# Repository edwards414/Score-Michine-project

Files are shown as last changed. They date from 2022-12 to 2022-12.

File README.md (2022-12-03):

# IoT Score Machine:Deep Leaning to predict score machine 
> **學校專題-成績辨識器**
>
> 影片介紹: [執行畫面](https://www.youtube.com/watch?v=YyPfOn3d-Wk)
>
>研究動機: 為改善目前登記成績的速度以及大資料的整理



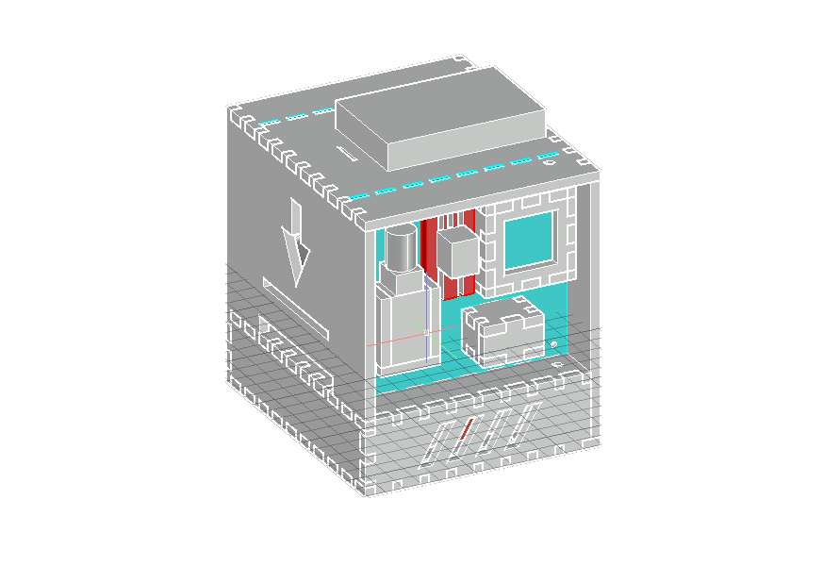
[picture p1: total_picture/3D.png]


## 結構設計
>   
> 設計 : [分解環繞影片](https://www.youtube.com/watch?v=SSCol9JbORs)
> 
在影片中我的捲軸系統是利用兩串小輪胎加上齒輪然後使用減速馬達將它帶動,辨識區域是利用伺服馬達來控制倒紙作業,整個結構是利用雷射切割完成,使用的軟體是AutoCAD,整個作品使用了2D組裝的思維藉由卡扣連接設計進行
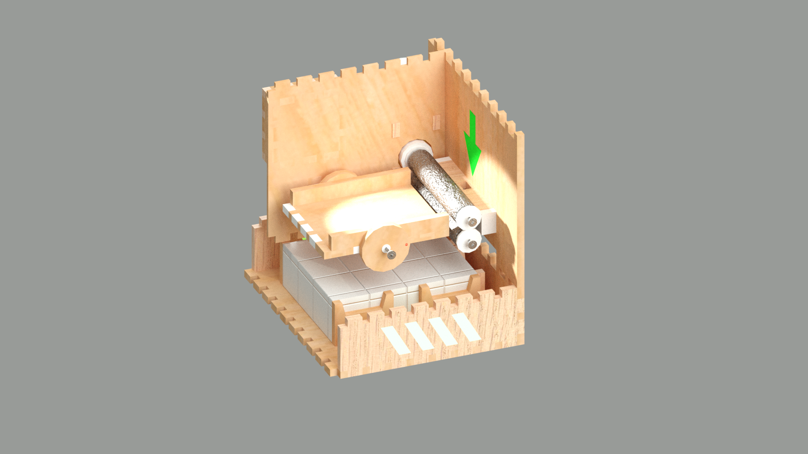
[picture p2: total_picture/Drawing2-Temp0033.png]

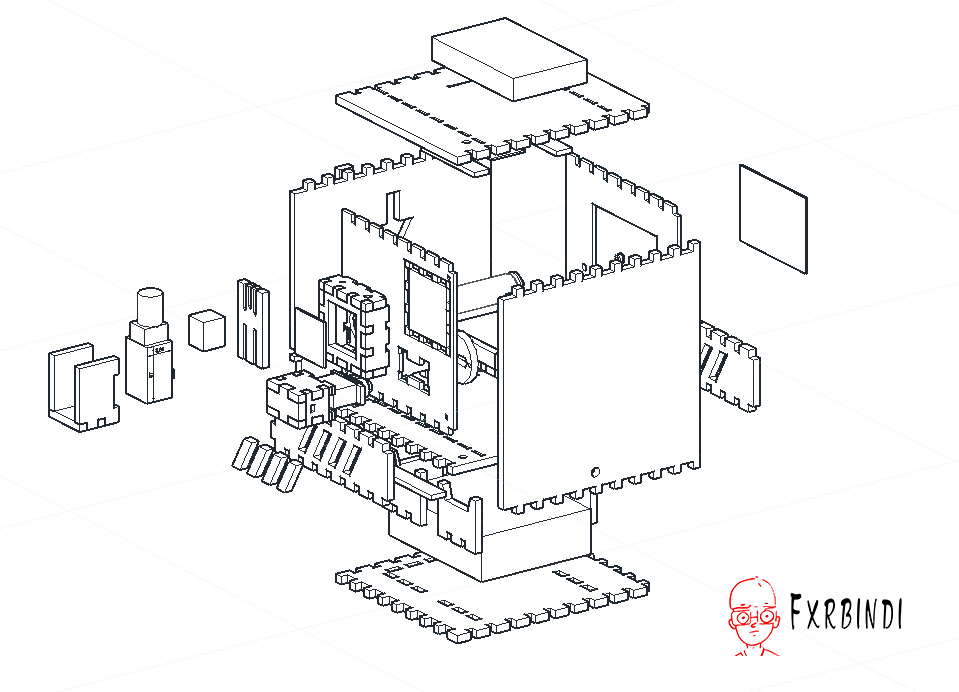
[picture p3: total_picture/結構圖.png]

> 草稿圖

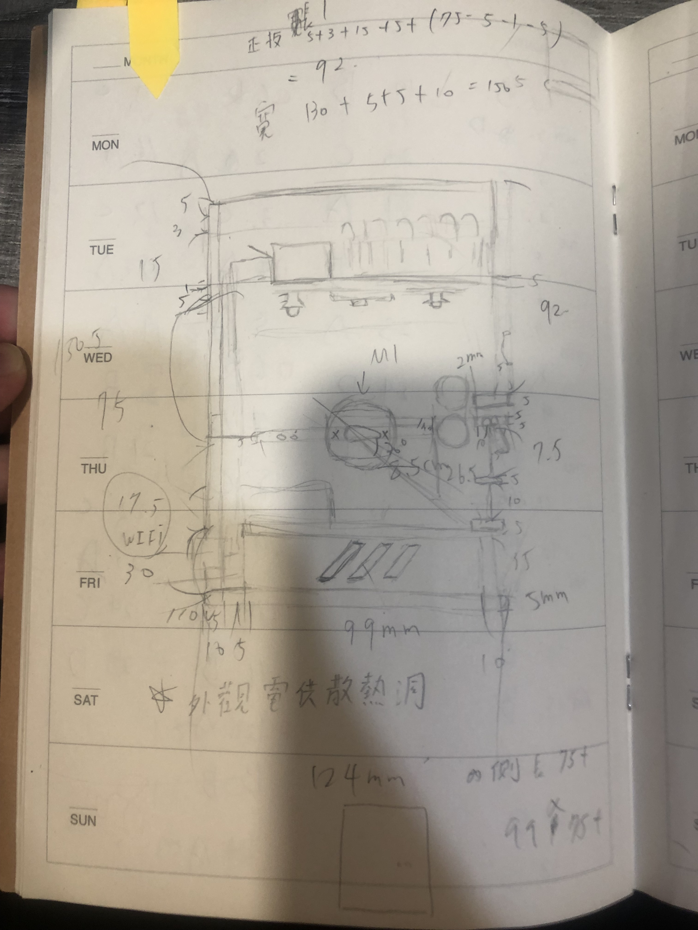
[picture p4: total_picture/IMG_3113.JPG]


> 捲軸系統

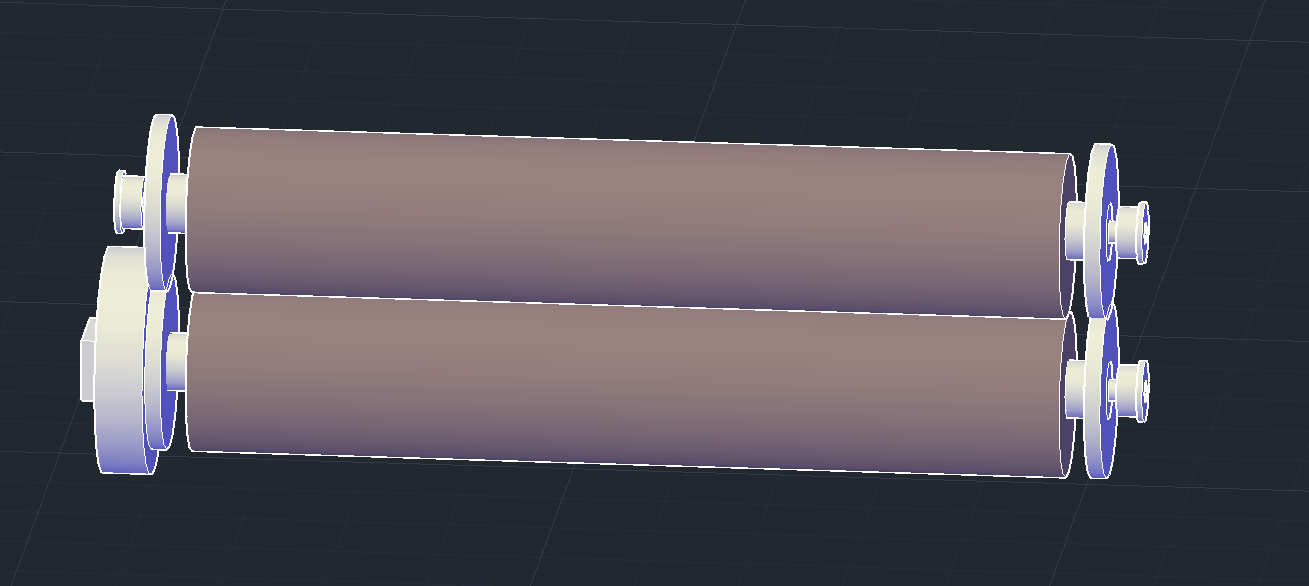
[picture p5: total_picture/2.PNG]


## 使用器具

- 主要硬體
  - Raspberry pi 3b+
  - 減速馬達
  - 伺服馬達(mg90s)180度
  - 3.3v 轉5v電位邏輯轉換器(T74)
  - 紅外線巡跡模組(FC123) *2
  - LED燈條(WS2812)*4
  - 繼電器5v
  - AC110-DC5V電源供應
- 軟體
  - Visual Studio Code
  - AutoCad
  - Adobe Illustrator 2022
  - Adobe Photoshop 2021
  - FileZilla
- 語言
  - python
  - javascript
  - html
  - css
  - javascript
  - bootscript

## 網頁設計
 
我使用了google-excel(當成資料庫),利用javascript讀取資料庫並在網頁上面呈現,網頁可以對成績表做查詢,也做RWD設計讓各個裝置都可以使用

> 網站介紹: [點我!!查詢請輸入【段考二】](https://script.google.com/macros/s/AKfycbwUPB8av8gJiDm0B71revtbjKE4klsRZkYY4DOG9oE/dev)

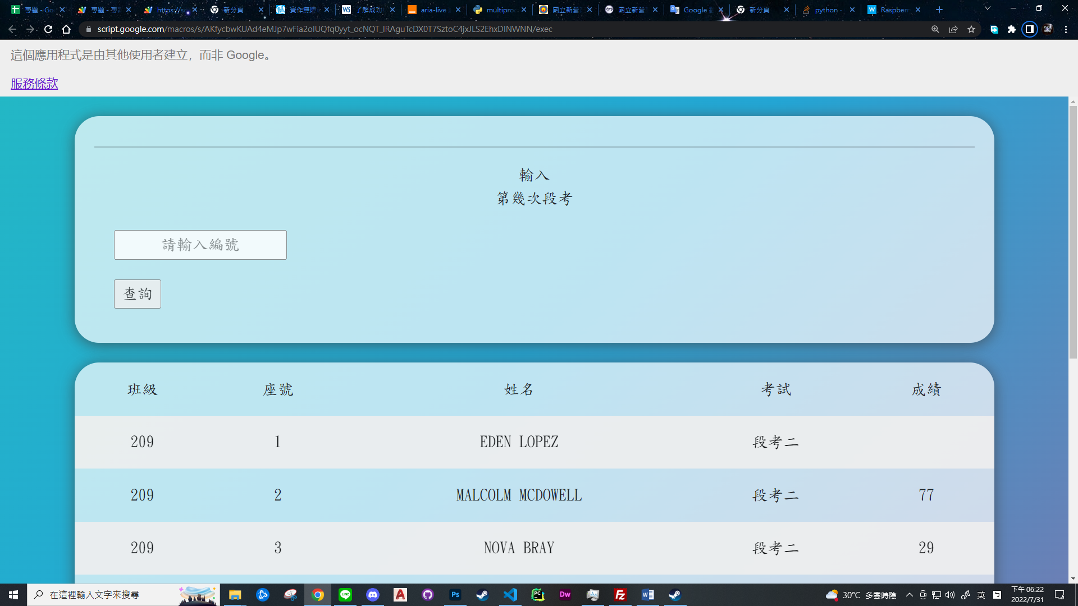
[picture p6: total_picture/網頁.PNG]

> 
>使用google-api讓python能與google-excel連結
>

## 使用方法/示例

```python
gc = pygsheets.authorize(service_account_file='project.json')
survey_url = 'your google-excel url'
sh = gc.open_by_url(survey_url)
ws = sh.worksheet_by_title('text')#你的試算表名稱
```
取得憑證(.join的檔案)後,python讀取join檔後利用這個檔案與google-api進行驗證,之後就可以操控試算表了

> [原作網址](https://hackmd.io/@Yun-Cheng/GoogleSheets)

## 關於辨識系統
> 深度學習
> 卷積神經網路(Convoluational Neural Network)
> 訓練庫 經典的手寫數字資料集【Mnist】

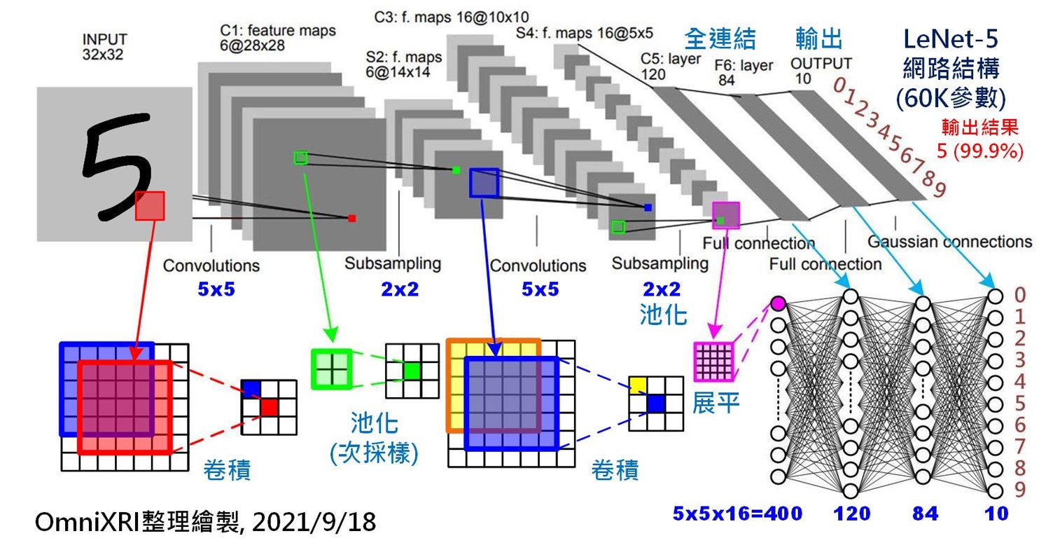
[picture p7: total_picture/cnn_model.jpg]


- [原作:OmniXRI](https://ithelp.ithome.com.tw/m/articles/10266628?sc=rss.iron)

Cnn是用來影像辨識的,它的功能用起來就像,假如我們看見一個人我們要怎麼判斷是不是人,在我們的大腦中,眼睛會先透過把看見的東西傳回腦袋,然後我們的大腦會進行特徵的擷取並與我們認知人的特徵做對比,進行對比後發現有部分軌跡形狀相似,我們就會認為他是一個人,在電腦中是輸入,卷積層,池化層,卷積層,池化層,壓平,傳入神經元進行分析輸出0-9的機率

如何在python中使用cnn,我們會在程式中建立cnn模型,把圖片正規化,後把資料丟進去訓練,把訓練完的權重(Weights)儲存,再用訓練好的權重套到(load_weights)模型上對圖片進行預測(predict)

> 卷積模型(model)

```python
def CNN_model():
    model = keras.Sequential(name="CNN") 
    model.add(layers.Conv2D(16,(5,5),activation='relu',padding='same',input_shape=(28,28,1))) #第一層輸入
    model.add(layers.MaxPooling2D((2,2)))
    model.add(layers.Conv2D(32,(5,5),padding='same',activation='relu'))
    model.add(layers.MaxPooling2D((2,2)))
    model.add(layers.Dropout(0.25))
    model.add(layers.Flatten())#轉一維陣列
    model.add(layers.Dense(128,activation="relu"))
    model.add(layers.Dropout(0.5))
    model.add(layers.Dense(10,activation='softmax')) #0-9輸出
    model.compile(optimizer='adam',
               loss=tf.losses.SparseCategoricalCrossentropy(from_logits=True),
               metrics=['acc'])
    return model
```
> 訓練結果

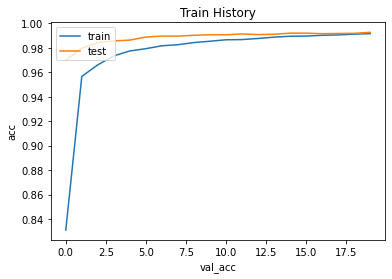
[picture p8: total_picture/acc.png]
  
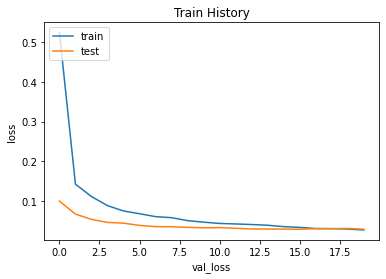
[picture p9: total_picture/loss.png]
   

> 驗證正規化(Normalization)的過程
正規化是一個在進入卷積神經網路模型之前的一個程序主要工作是將圖片改成固定格式的二維陣列

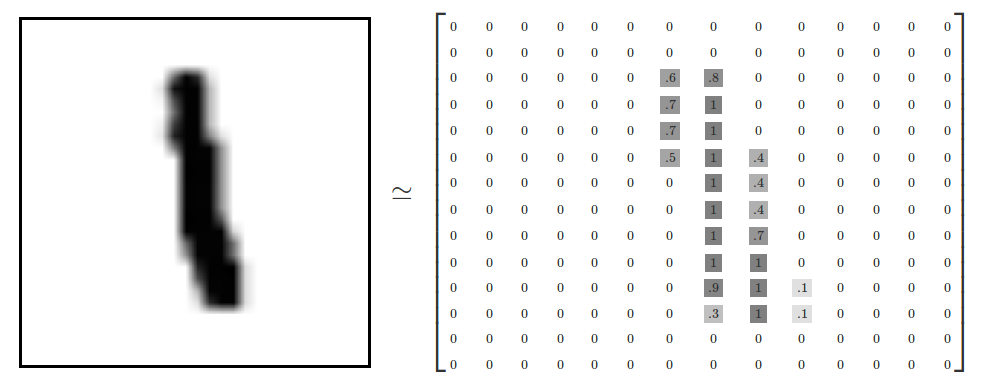
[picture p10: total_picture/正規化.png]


>為什麼要求證?

A:因為在進行卷積模型訓練時,我發現我丟我自己的圖片進入cnn_model進行預測,預測出來的答案與我寫的數字不一樣所以我針對正規化這個部分下去做驗證看是否在input時就有問題了

> 
> 我使用了python把程式中正規化的部分逐一填入excel
> 
> 這樣就可以在excel中圖像化
> 
> 在編輯器中無法將正規化print出來所以才使用excel作為輔助

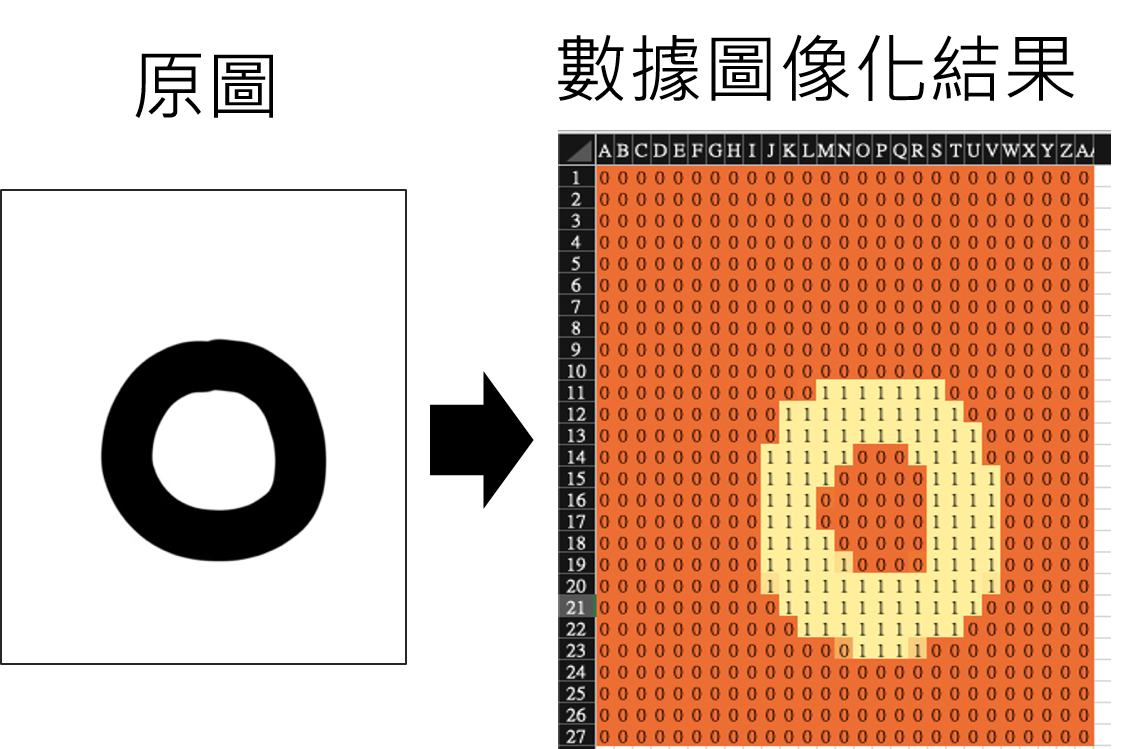
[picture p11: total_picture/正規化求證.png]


## 影像處理 

- 紙張進入後利用綠光加藍光把紅色變成黑色之後用高對比把線條的輪廓加深

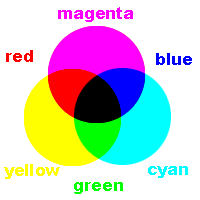
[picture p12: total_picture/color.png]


- 經過侵蝕圖片的方式把小點都處理掉

- 取得圖片的輪廓進行正方形的截圖

- 對每個數字切割

> 拍攝紙張

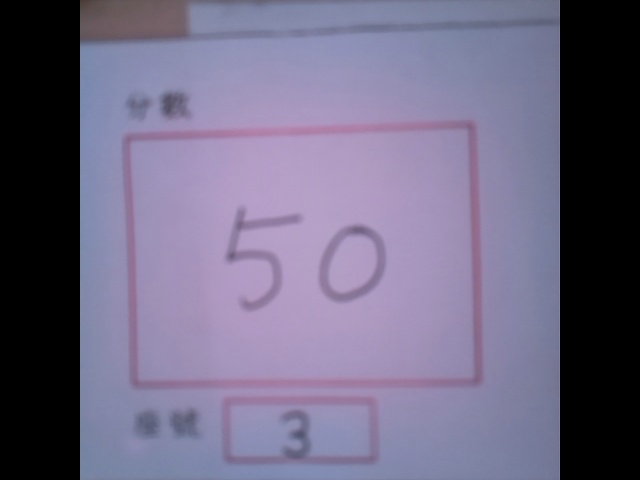
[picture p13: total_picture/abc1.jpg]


> 處理

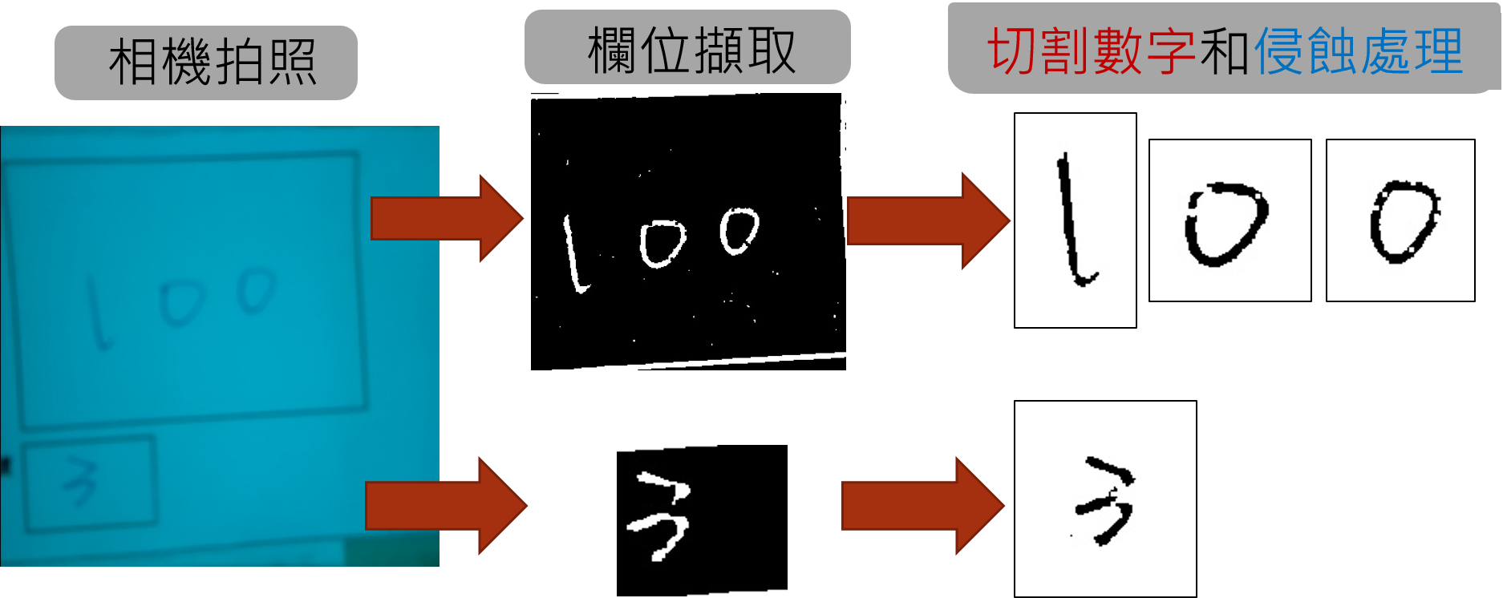
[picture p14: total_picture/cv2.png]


本來是用HSV下去做顏色的判斷後來發現不管怎麼調,截出來圖片都是一團亂,也有用YUV色彩去抓顏色,也是因為YUV對紅色及藍色有較好的辨識度所以才會用紅框,後來調光源發現在白光的照亮下我的圖上白色的部分有很多的粉紅色的光影,所以就朝著透過光源的方向去讓圖片處理得更好 

更好的方式:霍華夫取線(是一個ai對直線的算法,使用這個算法可以使圖片提取更完整)
## 線路圖

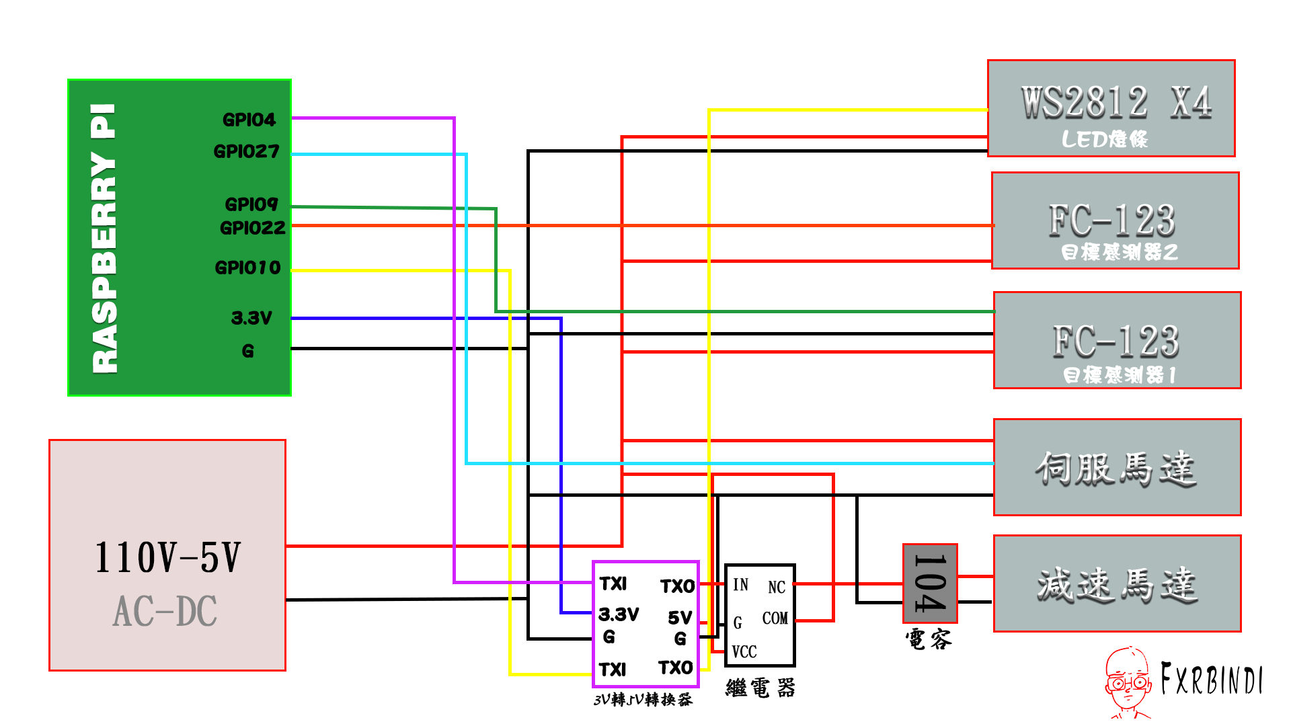
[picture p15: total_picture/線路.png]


> CAD模擬各零件擺放

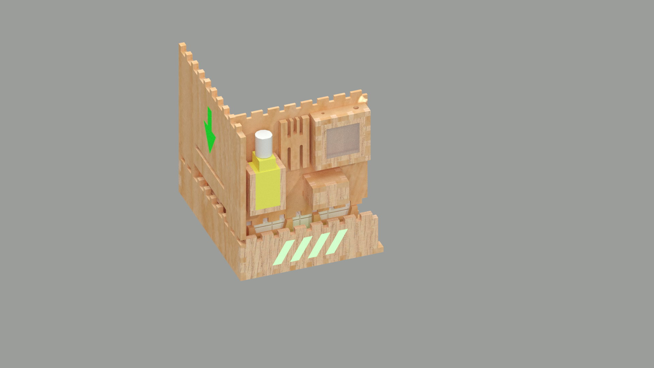
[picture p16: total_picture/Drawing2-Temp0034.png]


> 實際主裝

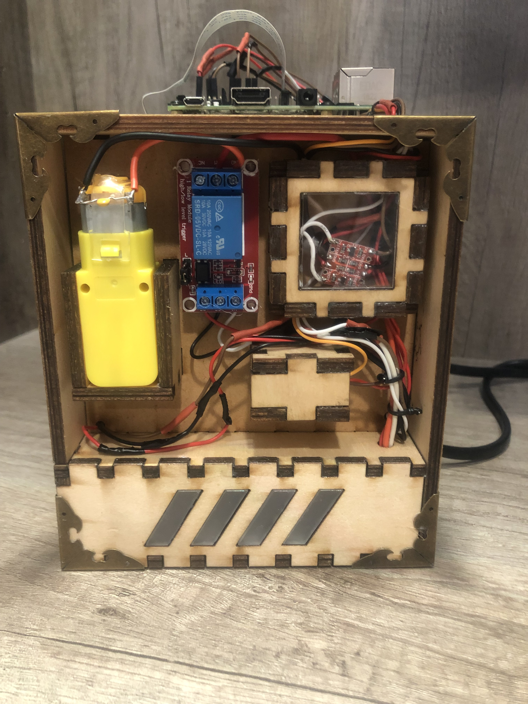
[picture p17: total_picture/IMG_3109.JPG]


## 流程程式

> 初始化
> 
> 接著呼叫FC123 loop定義
> 
> 執行拍照截圖處理..等程序
> 
> except除錯程序控制燈號警示我們
> 

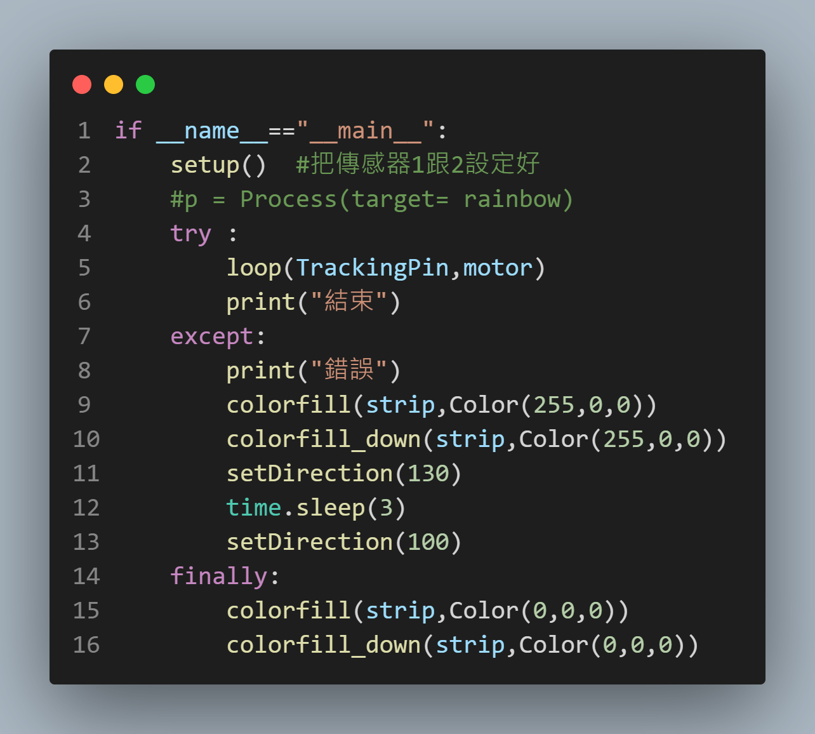
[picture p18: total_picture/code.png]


## 處理問題

> 伺服馬達抖動問題
> 
> WS2812 LED燈條五秒鐘後出現白光-不受控制
> 
> PMIC 損毀

### 1.伺服馬達抖動問題

> 可能的問題是軟體模擬pwm波會有誤差值,每一個伺服馬達的誤差值都不一樣,假如開發版發出來的誤差值大於伺服馬達給出的誤差值就會出現抖動的問題

我們一剛開始應先從程式的部分下手,因為我們所用的mg90s它是屬於較便宜的馬達所以它的誤差值沒有像步進馬達那些更高階的馬達小,所以不太會因為誤差而抖動

伺服馬達的功能與金錢成正比!!

> 伺服馬達原理(型號：mg90s)

伺服馬達是利用pwm去控制轉舵要轉幾度

 > 什麼是pwm ? 

分為硬體pwm、軟體pwm控制(現在使用的是軟體pwm)

 led燈有開跟關兩個狀態我們都是利用pin腳輸出高電壓(3.3v)或者低電壓(0v)來控制,但我們的伺服馬達有0～180度有180種狀態,所以就要使用pwm作為控制,pwm也是一種輸出高低電壓的原理,但他是使用高低電壓的時間差作為一種訊號

電源頻率50HZ,脈衝寬度500us-2500us 

1s = 1000ms ,1ms = 1000us

我們由電源頻率得知工作週期為20ms

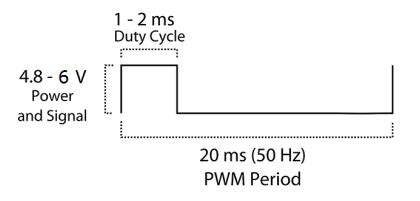
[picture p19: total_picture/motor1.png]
 

伺服馬達脈衝寬度調變訊號
（Servo PWM Singal）

各角度所需要的脈衝寬度

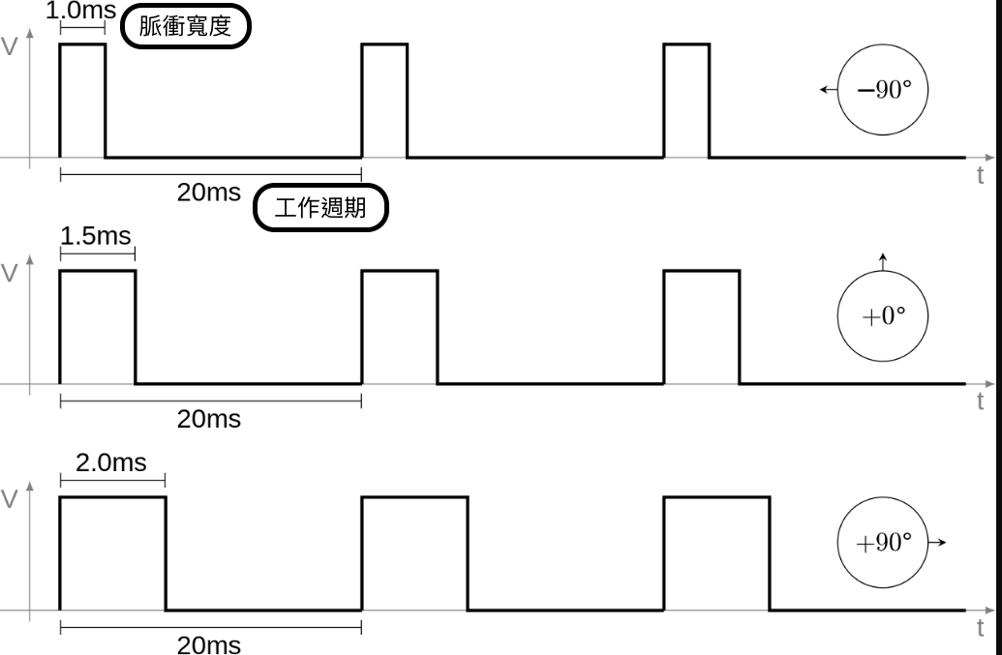
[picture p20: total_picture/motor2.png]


> code
```python
#coding:utf-8
import pigpio
import RPi.GPIO as GPIO
import time
pin_servo = 27
# 終端機需輸入(才能執行pigpiod)
# sudo systemctl enable pigpiod
pwm = pigpio.pi()
pwm.set_mode(pin_servo, pigpio.OUTPUT)
pwm.set_PWM_frequency(pin_servo, 50)  # 50Hz frequency
def destroy():
    pwm.set_PWM_dutycycle(pin_servo, 0)
    pwm.set_PWM_frequency(pin_servo, 0)
# 輸入0 ～ 180度即可
# 別超過180度
def setDirection(angle):
    # 0 = 停止轉動
    # 500 = 0度
    # 1500 = 90度
    # 2500 = 180度
    duty = 500 + (angle / 180) * 2000
    pwm.set_servo_pulsewidth(pin_servo, duty)
    print("角度=", angle, "-> duty=", duty)
setDirection(100)
time.sleep(5)
setDirection(130)
#time.sleep(5)
#setDirection(100)
```
### 2.WS2812 LED燈條問題
由於WS2812 LED-Strips需要高精準度的時脈,只要接收到的訊號有錯誤就會馬上亮白光,所以我們需要透過更改系統檔的方式更改CPU的頻率,否則SPI會頻率錯誤



> 解決方式: [點我](https://dordnung.de/raspberrypi-ledstrip/ws2812)
> Video: [SPI錯誤](https://youtube.com/shorts/EJO2xfDEh9g)

### 3.PMIC 損毀

> 這次專題中出現了兩次的晶片(PMIC)損壞

> PMIC 損壞會導致樹梅派不能開機和3.3V短路

1.	我以為HDMI是熱插拔的,所以在運行時直接拔除導致PMIC損壞
2.	在量PIN角電壓時,不小心讓5V和3.3V誤接,導致3.3V短路

> 解決方案:請專人更換PMIC(大概台幣800元)

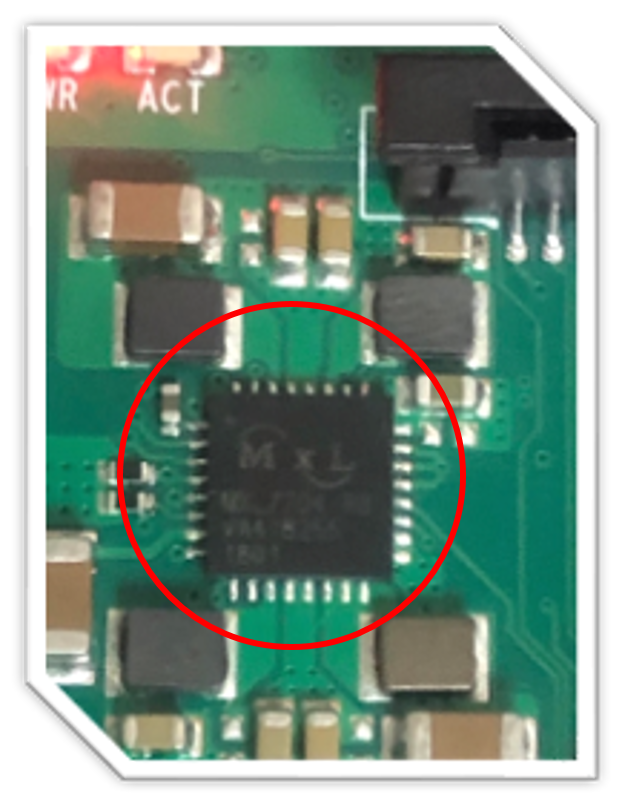
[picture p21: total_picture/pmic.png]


> 可以改進的部分

 1.	在網頁中可以使用後端PHP和MYSQL去控制,做出更多的介面,和成績的分析,或者加入權限登入系統等等功能

 2.	在機器中倒紙的部分當初沒有考慮過摩擦係數的問題導致紙張本來要從前面出來的變成從後面出來,可以更改的方向是更換較光滑的材質,或者利用馬達加上橡膠的方式去把紙推出

 3.	CNN辨識的準確率,在辨識率的方面因為環境的因素有些圖片有些可能辨識不出來但還是有大概98%的準確性,可以改善問題的方式是在CNN MODEL中加入pre-train model,使用機器處理出來的圖片進行訓練

 4.	圖片處理上可以做得更好，處理線條的方式可以使用霍夫變換提取直線，會比起顏色提取好

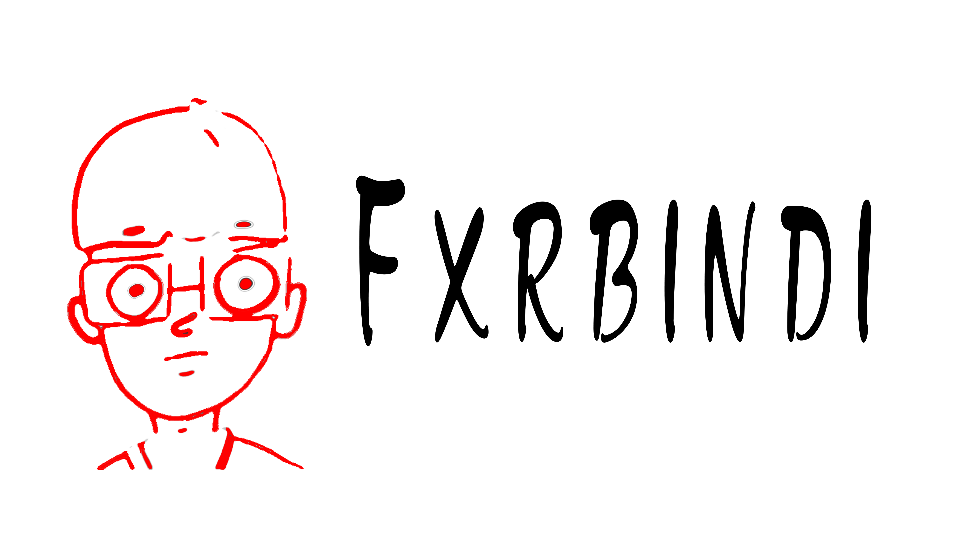
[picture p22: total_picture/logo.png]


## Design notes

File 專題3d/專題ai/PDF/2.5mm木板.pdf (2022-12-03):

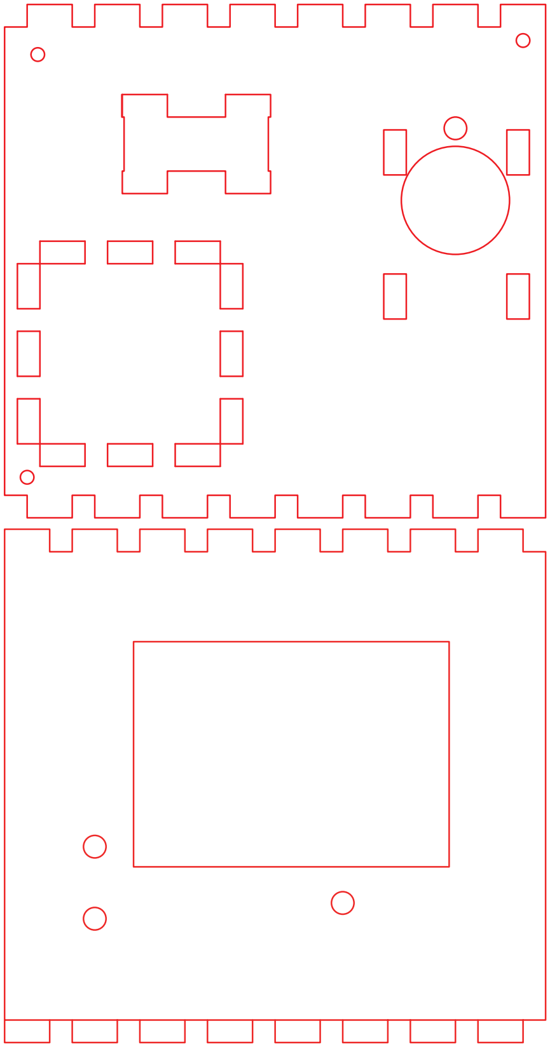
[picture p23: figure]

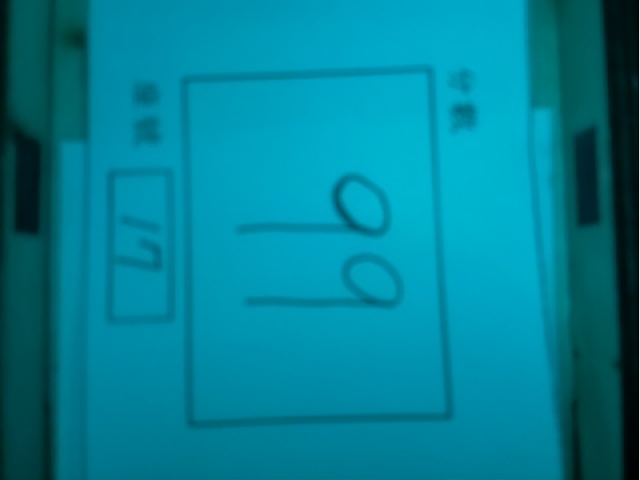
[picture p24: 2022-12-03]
project/picture/abc.jpg

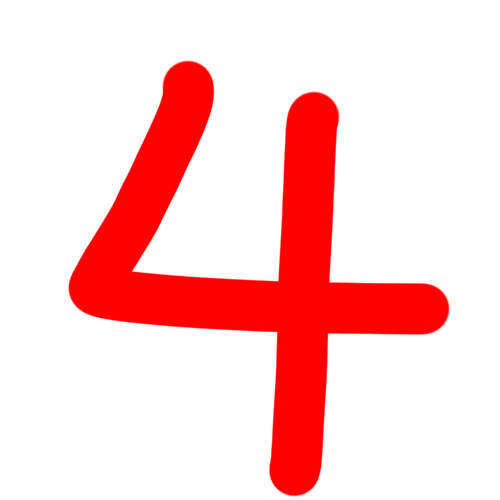
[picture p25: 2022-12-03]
total_picture/n4.jpg

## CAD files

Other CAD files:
專題3d/2d專題.dwg
專題3d/渲染.dwg
專題3d/Drawing4.dwg
專題3d/Drawing3.dwg
專題3d/結構補件5mm木板.dwg

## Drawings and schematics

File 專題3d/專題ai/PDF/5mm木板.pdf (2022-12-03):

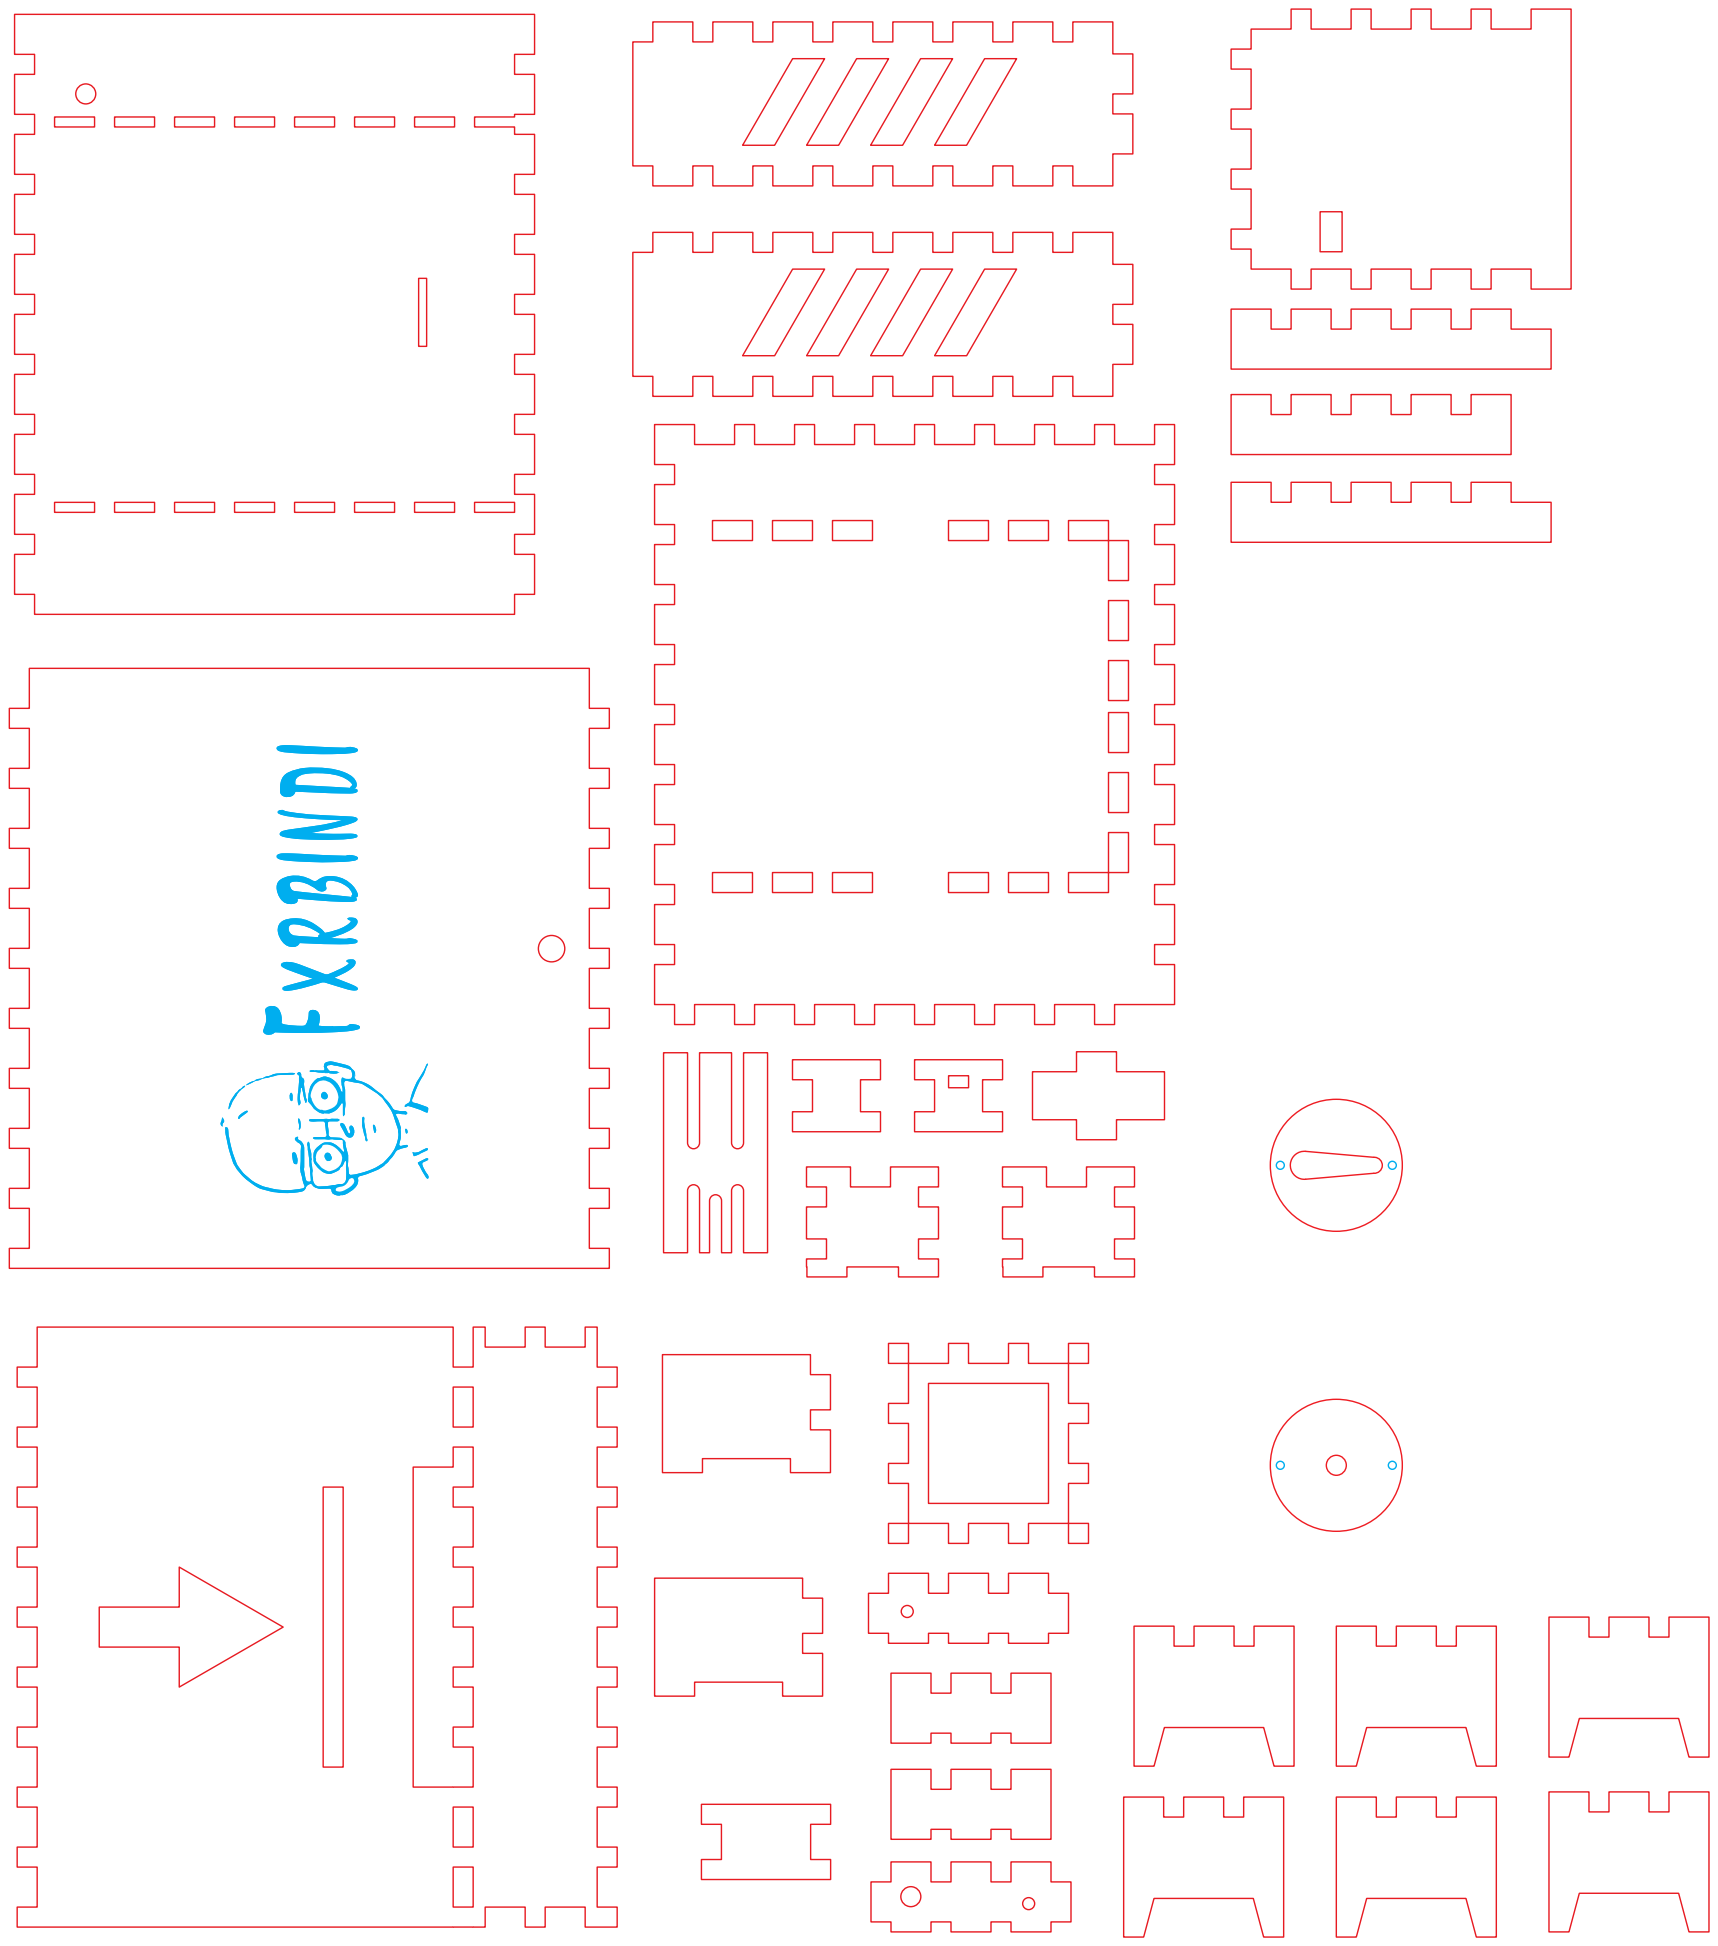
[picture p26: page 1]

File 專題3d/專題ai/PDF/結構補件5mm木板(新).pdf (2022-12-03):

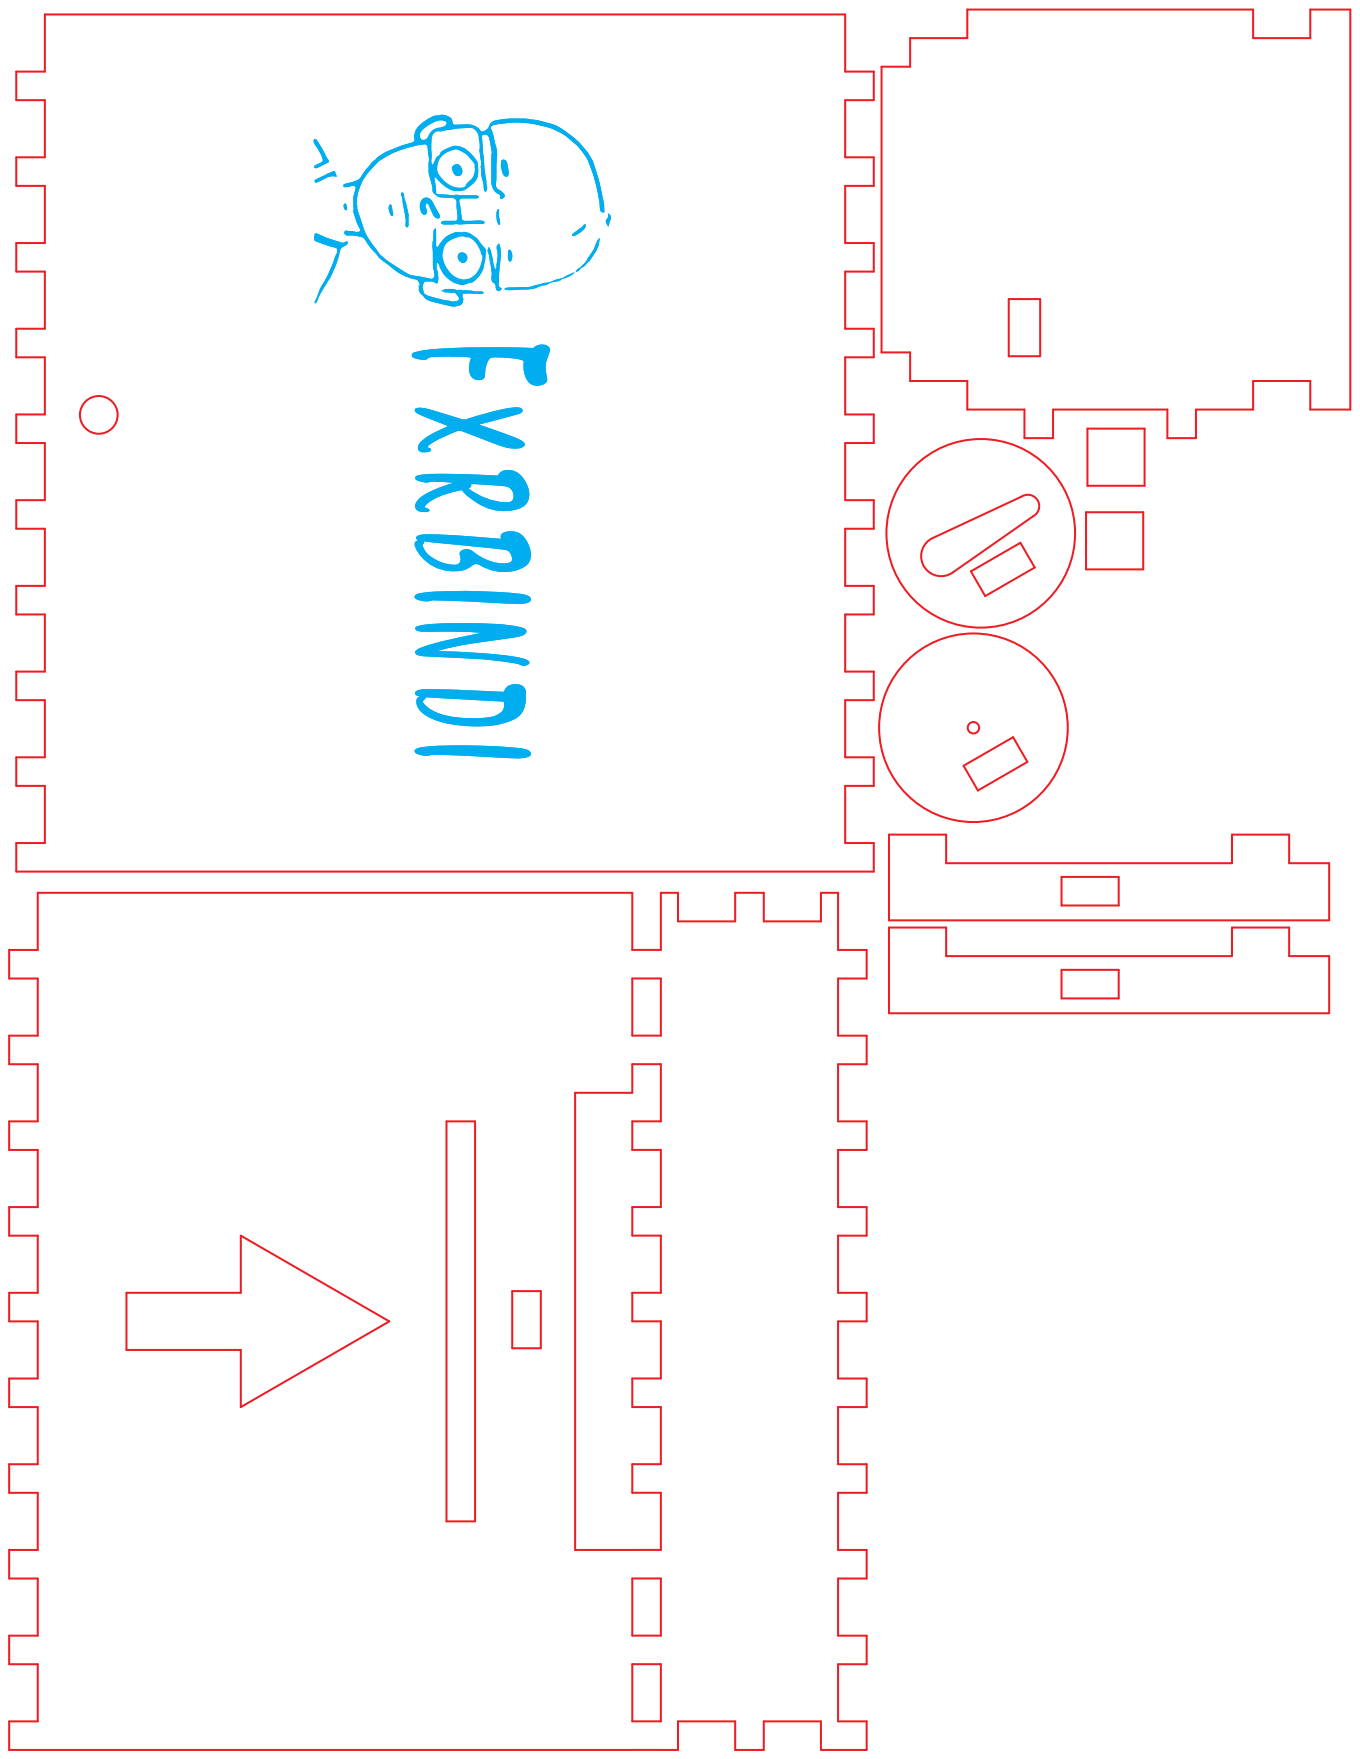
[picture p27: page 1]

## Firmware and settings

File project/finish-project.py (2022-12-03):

from tensorflow.keras import layers
import tensorflow as tf
from tensorflow import keras
import cv2
import numpy as np
#-----------------
import pygsheets
import pandas as pd
#-----------------------------
import board
import neopixel
import pigpio
import RPi.GPIO as GPIO
from gpiozero import LED
import time
from multiprocessing import Process
# 将服务设置为开机启动
# sudo systemctl enable pigpiod
from rpi_ws281x import PixelStrip, Color
import argparse
from multiprocessing import Process
#--------------------------------
LED_COUNT = 32        # Number of LED pixels.
#LED_PIN = 18          # GPIO pin connected to the pixels (18 uses PWM!).
LED_PIN = 10        # GPIO pin connected to the pixels (10 uses SPI /dev/spidev0.0).
LED_FREQ_HZ = 800000  # LED signal frequency in hertz (usually 800khz)
LED_DMA = 10          # DMA channel to use for generating signal (try 10)
LED_BRIGHTNESS =230  # Set to 0 for darkest and 255 for brightest
LED_INVERT = False    # True to invert the signal (when using NPN transistor level shift)
LED_CHANNEL = 0       # set to '1' for GPIOs 13, 19, 41, 45 or 53

TrackingPin = 22 #感測器1
TrackingPin2 = 9 #感測器2
motor=LED(4) #馬達
pin_servo = 27 #伺服馬達
pwm = pigpio.pi()
pwm.set_mode(pin_servo, pigpio.OUTPUT)
pwm.set_PWM_frequency(pin_servo, 50)  # 50Hz frequency
#LED-------------
parser = argparse.ArgumentParser()
parser.add_argument('-c', '--clear', action='store_true', help='clear the display on exit')
args = parser.parse_args()
strip = PixelStrip(LED_COUNT, LED_PIN, LED_FREQ_HZ, LED_DMA, LED_INVERT, LED_BRIGHTNESS, LED_CHANNEL)
strip.begin()
#----------------
def destroy():
    pwm.set_PWM_dutycycle(pin_servo, 0)
    pwm.set_PWM_frequency(pin_servo, 0)
def setDirection(angle):
    duty = 500 + (angle / 180) * 2000
    pwm.set_servo_pulsewidth(pin_servo, duty)
    print("角度=", angle, "-> duty=", duty)
def setup():
    GPIO.setmode(GPIO.BCM)
    GPIO.setup(TrackingPin, GPIO.IN, pull_up_down=GPIO.PUD_UP)
    GPIO.setup(TrackingPin2, GPIO.IN, pull_up_down=GPIO.PUD_UP)
    motor.off()
    setDirection(100)
    colorfill(strip,Color(0,0,0))
    colorfill_down(strip,Color(0,255,0))
def loop(TrackingPin,motor):
    
    while True:
        if GPIO.input(TrackingPin) == GPIO.HIGH:
            colorfill_down(strip,Color(255,0,0))
            print ('目前偵測到1')
            #colorfill(strip,Color(0,255,255))
            motor.on()
            time.sleep(2)
            motor.off()
            loop2(TrackingPin2)
            break
def loop2(TrackingPin2):
    while True:
        if GPIO.input(TrackingPin2) == GPIO.HIGH:
            print ('目前偵測到2')
            colorfill(strip,Color(0,255,255))
            camar_take_pic()
            setDirection(130)
            time.sleep(3)
            setDirection(100)
            break
        else:  
            print("沒有偵測到2")  
            loop(TrackingPin,motor,xasd) #給錯誤跳出迴圈
#----------------
#燈光
def colorfill(strip,color):
    count=16
    for i in range(16):
        strip.setPixelColor(i+count, color)
        strip.show()
def colorfill_down(strip,color):
    for i in range(16):
        strip.setPixelColor(i, color)
        strip.show()
def wheel(pos):
    if pos < 85:
        return Color(pos * 3, 255 - pos * 3, 0)
    elif pos < 170:
        pos -= 85
        return Color(255 - pos * 3, 0, pos * 3)
    else:
        pos -= 170
        return Color(0, pos * 3, 255 - pos * 3)
def rainbow( wait_ms=20, iterations=1):
    global strip
    while True:
        for j in range(256 * iterations):
            for i in range(16):
                strip.setPixelColor(i, wheel((i + j) & 255))
            strip.show()
            time.sleep(wait_ms / 1000.0)
        
#-----------------
#cv2.imshow

def camar_take_pic():
    cap = cv2.VideoCapture(0)
    ret, frame = cap.read()
    frame = rotate_img(frame)    
    cv2.imwrite('abc.jpg',frame)
    digital_recognition_and_updata_WEB('abc.jpg') #辨識到上傳
    print("已照相")
    cap.release()
def rotate_img(img): #圖片旋轉
    (h, w, d) = img.shape # 讀取圖片大小
    center = (w // 2, h // 2) # 找到圖片中心
    # 第一個參數旋轉中心，第二個參數旋轉角度(-順時針/+逆時針)，第三個參數縮放比例
    M = cv2.getRotationMatrix2D(center, 90, 1.0)
    rotate_img = cv2.warpAffine(img, M, (w, h))
    
    return rotate_img
#------------------------------------
gc = pygsheets.authorize(service_account_file='project.json')
survey_url = 'https://docs.google.com/spreadsheets/d/1Q8oc9Y7EACEgQzROZuCZDBGK2Z28XPk6cEC_6r5P5Hk/edit#gid=0'
sh = gc.open_by_url(survey_url)
ws = sh.worksheet_by_title('text')

def red_b(img,contours):
    for i in range (0,len(contours) ):
        x,y,w,h = cv2.boundingRect(contours[i])
        #print(x,y,w,h)
        cv2.rectangle(img,(x,y),(x+w,y+h),(0,0,255),2)
   # camar(img)
#def camar(img):
 #   cv2.imshow(str(img),img)
  #  cv2.waitKey(5000)
  #  cv2.destroyAllWindows()
    
#-----------------
def red_boder(img):
    w,h,c = img.shape #抓取圖片寬高
    x,y,contrast,brightness = 50,0,200,0 
    crop_img = img[y:y+h, x+50:x+w-20]  #縮小圖片
    output = crop_img * (contrast/127 + 1) - contrast + brightness # 轉換公式
    output = np.clip(output, 0, 255)#增加對比200%
    output = np.uint8(output)
    gray_img = cv2.cvtColor(output, cv2.COLOR_BGR2GRAY) #把圖片轉成灰階
    th1 = cv2.adaptiveThreshold(gray_img, 255, cv2.ADAPTIVE_THRESH_MEAN_C,\
        cv2.THRESH_BINARY, 11, 2) #二值化
    kernel = np.ones((3,3),np.uint8)
    dilate = cv2.dilate(th1,kernel,iterations = 1) #影像侵蝕
    ret, th1 = cv2.threshold(dilate, 127, 255, cv2.THRESH_BINARY_INV) #黑白調換
    #camar(th1)
    img = cv2.cvtColor(th1,cv2.COLOR_GRAY2BGR)#轉BGR
    contours,hierarchy = cv2.findContours(th1,cv2.RETR_EXTERNAL,cv2.CHAIN_APPROX_SIMPLE) #找輪廓
    for i in range (0,len(contours)):
        x,y,w,h = cv2.boundingRect(contours[i])
        filename=0 #檔名
        totle=[]#計算xy順序
        for i in range(0,len(contours)):
            x,y,w,h = cv2.boundingRect(contours[i])
            if w*h>5000 and w>100:
                totle.append([x,y,w,h])
                totle = sorted(totle,key =(lambda totle:totle[1]))
                #print(totle)
        for i in range(0,len(totle)):
            x,y,w,h = totle[i]
            if i==0:
                crop_img = img[y+50:y+h-50,x+30:x+w-50]
            else:
                crop_img = img[y+8:y+h-8, x+10:x+w-10]
            cv2.imwrite("number//red_boder//"+str(filename)+'.jpg', crop_img)
            filename+=1 
    return filename
def cut_pic(img,i):   #圖片跟目前讀取的圖片
    img = cv2.cvtColor(img,cv2.COLOR_BGR2GRAY)
    contours,hierarchy = cv2.findContours(img,cv2.RETR_EXTERNAL,cv2.CHAIN_APPROX_SIMPLE)#只檢查外輪廓
    #print('共有多少個輪廓',len(contours),'目前看的圖',i)
    filename=0
    #red_b(img,contours)
    totle = []#順序
    for s in range(0,len(contours)): #共兩大塊
        x,y,w,h = cv2.boundingRect(contours[s]) #輪廓xy 寬高
        if w*h>800: 
            totle.append([x,y,w,h])
            totle = sorted(totle, key=(lambda totle:totle[0]))
            #print("totle",totle)
    #red_b(img,totle)
    for i1 in range (0,len(totle)):
        x,y,w,h = totle[i1]
        crop_img = img[y:y+h, x:x+w]
        if i==0:
            crop_img = cv2.copyMakeBorder(crop_img,20,20,20,20,cv2.BORDER_CONSTANT,value=[0,0,0]) 
            cv2.imwrite('number//score//'+str(filename)+'.jpg',crop_img )
            filename+=1
        elif i==1:
            #print('number//score//'+str(s)+'.jpg')
            crop_img = cv2.copyMakeBorder(crop_img,30,30,30,30,cv2.BORDER_CONSTANT,value=[0,0,0]) #因為太小所以要要外擴
            cv2.imwrite('number//seat_number//'+str(filename)+'.jpg', crop_img)
            filename+=1 
    #print('pic_size_check',pic_size_check)
    return  filename
def red_boder_data_open_and_deal(contours): #大區域切小塊
    k=[] #照片的數量 #0為座號
    #print("共有大塊",contours)
    for i in range(0,contours):
        img = cv2.imread("number//red_boder//"+str(i)+".jpg")
        img_totle=cut_pic(img,i)
        k.append(img_totle)
    return k 
opo = 0

def picchangesize(img):
    global opo
    img = img[:,:,0]
    ret, img = cv2.threshold(img,150,255, cv2.THRESH_BINARY_INV)#轉二值化
    cv2.imwrite('picture//'+str(opo)+'.jpg',img)
    opo+=1
    img2_gray = img#cv2.cvtColor(img,cv2.COLOR_BGR2GRAY) #轉成黑白
    img3 = 255 - img2_gray #黑白調換
    img3 = img3.astype('float32')
    img3_min = np.amin(img3)#0.0
    img4 = img3 - np.amin(img3) #圖片上像素的01
    img5 = 255 * img4 / (np.amax(img4)+1)
    kernel = np.ones((5,5),np.uint8)
    img6 = cv2.dilate(img5,kernel,iterations = 3)
    img7 = cv2.resize(img6,(28,28),1)
    img8 = img6.astype('uint8')
    x_test_image = np.reshape(img7,(1,28,28))
    x_Test4D = x_test_image.reshape(x_test_image.shape[0],28,28,1).astype('float32') #改變形狀
    x_Test4D_normalize = ( x_Test4D / np.amax(x_test_image) ) #除以像素最大值
    return x_Test4D_normalize

def CNN_model():
    model = keras.Sequential(name="CNN") 
    model.add(layers.Conv2D(16,(5,5),activation='relu',padding='same',input_shape=(28,28,1))) #第一層輸入
    model.add(layers.MaxPooling2D((2,2)))
    model.add(layers.Conv2D(32,(5,5),padding='same',activation='relu'))
    model.add(layers.MaxPooling2D((2,2)))
    model.add(layers.Dropout(0.25))
    model.add(layers.Flatten())#轉一維陣列
    model.add(layers.Dense(128,activation="relu"))
    model.add(layers.Dropout(0.5))
    model.add(layers.Dense(10,activation='softmax')) #0-9輸出
    model.compile(optimizer='adam',
               loss=tf.losses.SparseCategoricalCrossentropy(from_logits=True),
               metrics=['acc'])
    return model
def predict(CNN,img):
    x_Test4D_normalize = picchangesize(img)
    predict1 = CNN.predict(x_Test4D_normalize)
    #print("機率為",(max(predict1[0]))*100,"%")
    predicted = np.argmax(predict1,axis=1)
    #print("數字為",predicted[0])
    return predicted[0]
    #totle_number_list.append(predicted[0])

def list2number(list_n): #list裡面的數字轉數字
    n=len(list_n)
    totle=0
    for i in range(0,n):
        totle+=list_n[i]*(10**(n-i-1))
    if totle > 100:
        totle=100
    return totle
def digital_recognition_and_updata_WEB(img):
    CNN = CNN_model()
    CNN.load_weights('my_model_weights.h5')
    img = cv2.imread(str(img))
    contours=red_boder(img) #處理紅框
    pic_totle=red_boder_data_open_and_deal(contours) #處理切割
    seat_number=[]
    score=[]
    for i in range(0,pic_totle[1]): #座號
        img = cv2.imread("number//seat_number//"+str(i)+".jpg")
        n=predict(CNN,img)
        seat_number.append(n)  
    #print("--------------------")
    for i in range(0,pic_totle[0]): #分數
        img = cv2.imread("number//score//"+str(i)+".jpg")
        n=predict(CNN,img)
        score.append(n)
    #print("seat_number", seat_number)
    #print("score", score)
    seat_number = list2number(seat_number)
    score = list2number(score)
    print('seat_number',seat_number,'score',score)
    #print(str(score))
    ws.update_value('E'+str(seat_number+1), str(score))
#score = 0 #分數#換成分數
#if pic_totle==2:
#    score += totle_number_list[0]*10
#    score += totle_number_list[1]*1
#print("分數",score)
#cv2.waitKey(0)
#cv2.destroyAllWindows()

#---------------------------
if __name__=="__main__":
    setup()  #把傳感器1跟2設定好
    #p = Process(target= rainbow)
    try :
        loop(TrackingPin,motor)
        print("結束")
    except:
        print("錯誤")
        colorfill(strip,Color(255,0,0))
        colorfill_down(strip,Color(255,0,0))
        setDirection(130) 
        time.sleep(3)
        setDirection(100)
    finally:
        colorfill(strip,Color(0,0,0))
        colorfill_down(strip,Color(0,0,0))
        
        
    
    
    
#---------------------------

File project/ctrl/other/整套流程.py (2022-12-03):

import board
import neopixel
import pigpio
import RPi.GPIO as GPIO
from gpiozero import LED
import time
# 将服务设置为开机启动
# sudo systemctl enable pigpiod
TrackingPin = 22 #感測器1
TrackingPin2 = 9 #感測器2
motor=LED(4) #馬達
led_4=LED(2)
pin_servo = 27

pwm = pigpio.pi()
pwm.set_mode(pin_servo, pigpio.OUTPUT)
pwm.set_PWM_frequency(pin_servo, 50)  # 50Hz frequency
def destroy():
    pwm.set_PWM_dutycycle(pin_servo, 0)
    pwm.set_PWM_frequency(pin_servo, 0)
# 輸入0 ～ 180度即可
# 別超過180度
def setDirection(angle):
    # 0 = 停止轉動
    # 500 = 0度
    # 1500 = 90度
    # 2500 = 180度
    duty = 500 + (angle / 180) * 2000
    pwm.set_servo_pulsewidth(pin_servo, duty)
    print("角度=", angle, "-> duty=", duty)
def setup():
    GPIO.setmode(GPIO.BCM)
    GPIO.setup(TrackingPin, GPIO.IN, pull_up_down=GPIO.PUD_UP)
    GPIO.setup(TrackingPin2, GPIO.IN, pull_up_down=GPIO.PUD_UP)

def loop(pixels,TrackingPin,motor):
    x=0
    while True:
        if GPIO.input(TrackingPin) == GPIO.HIGH and x == 0:
            print ('目前偵測到')
            pixels.fill((0,255,0))
            pixels.show()
            motor.on()
            time.sleep(5)
            x=1
        elif GPIO.input(TrackingPin) == GPIO.HIGH and x == 1:
            motor.off()
            break
        else:    
            print ('沒有')
def loop2(TrackingPin2,led_4):
    while True:
        if GPIO.input(TrackingPin2) == GPIO.HIGH:
            print ('目前偵測到')
            led_4.on()
            time.sleep(7)
            led_4.off()
            setDirection(30)
            break
        else:    
            print ('沒有')
def destroy():
 GPIO.cleanup()
#-----------
#destroy()#清除針腳
length = 48
pixels = neopixel.NeoPixel(board.D10, length, brightness=0.1, auto_write=False,pixel_order=neopixel.RGB)
pixels.fill((255,0,0))
pixels.show()
setup()
loop(pixels,TrackingPin,motor)
loop2(TrackingPin2,led_4)
time.sleep(5)
setDirection(0)
pixels.fill((255,0,0))
pixels.show()
print("已完成")

#開啟綠燈
#偵測到後變紅燈,開起馬達結束
#偵測木板上的,偵測後開燈拍照
#伺服馬達送出紙張
#結束後燈光變綠



#https://learn.adafruit.com/circuitpython-on-raspberrypi-linux/installing-circuitpython-on-raspberry-pi
#pip3 install rpi_ws281x adafruit-circuitpython-neopixel
#python3 -m pip install --force-reinstall adafruit-blinka
